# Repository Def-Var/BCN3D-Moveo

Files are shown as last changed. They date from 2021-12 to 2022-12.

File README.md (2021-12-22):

# DefVar Moveo
This project is forked from [BCN3d MOVEO](https://github.com/BCN3D/BCN3D-Moveo). I changed some parts for my purposes so that I can rebuild this project six years after its creation.
Please check out my [blog](https://def-var.net) where I post weekly about this project.

## Changes

Changed in Motor type results in new 3M2C and 3M2CC use the new Version instead

## 3D printing settings 
layer height: 0.2 mm
Material: PLA 
Infill: 15% 

# Original Moveo README.md
In the following, there is the original text from the BCN3D MOVEO README.md

## BCN3D MOVEO

This is the repository that contains the CAD files, the STL files, the user manual (with the assembly manual), the firmware, and the Bill of Materials of the BCN3D Moveo.
BCN3D Technologies keeps taking important steps in order to achieve his goal of bringing the digital manufacturing technology to everyone. In this occasion we are presenting the BCN3D Moveo, a robotic arm design from scratch and developed by our engineers in collaboration with the Departament d’Ensenyament from the Generalitat de Catalunya. Its structure is fully printed using additive manufacturing technologies and its electronics are controlled by the software Arduino.
Moveo, fully functional nowadays, has been born, as all the BCN3D Technologies products, with an open and educational wish.

### Why BCN3D Moveo

One of the Departament d’Ensenyament worries is the high price of the materials the grade students must use on their internships. Holding that in mind, an Open Source robotic arm, adaptable by the students and low cost reproducible could take several educational itineraries: mechanical design, automatism, industrial programing, etc.
Thus, the BCN3D Moveo should allow the educational centers to enjoy a modifiable and easily accessible for the students, at a price far lower than the usual industrial equipment they used to have to acquire, with enough output for training purposes.
As a Fundació CIM area, BCN3D Technologies shares its educational vocation. That is the reason why when the Departament d’Ensenyament contacted us in order to suggest and offer this project a year ago we didn’t hesitate on taking that opportunity.
Once we had the robotic arm designed and manufactured we started the last phase of the project, which consisted on an assembling and fine tuning workshop for 15 institutes around Catalonia, which took place in the BCN3D Technologies.
These institutes already have the BCN3D Moveo in their classrooms and workshops, and will have to present an internship program that proves their knowledge about the arm during September.

### Open Source Technology: Github

As we have done with all our developed produtcs, the BCN3D Moveo files will be available for everyone. Thanks to the platform Github, a website where users around the world share their designs, anyone will be able to obtain all the necessary information in order to assemble his own BCN3D Moveo at home.

Unlike the other BCN3D products, the Moveo won’t be commercialized. The project has been born and developed in order to make a move for the community progress starting from the Departament d’Ensenyament idea.
Nevertheless, BCN3D will fee all the Moveo know how on our Github account, as we have been doing with all the BCN3D Technologies products. Thus, the users will be able to find the bill of material (BOM), where all the needed components for the assembling of the arm come detailed, as the CAD designs, so anyone will be able to modify the BCN3D Moveo design as they wish.
Furthermore, the Github users will find the STL files for the structure printing and the assembling, fine tuning and firmware upload manuals, which will be available both in English and Spanish.

### Acknowledgements

This project is based on a project by [Andreas Hölldorfer](http://chaozlabs.blogspot.de/). You can see his original project on [Hackaday.io](https://hackaday.io/project/3800-3d-printable-robot-arm), [Github](https://github.com/4ndreas/BetaBots-Robot-Arm-Project/tree/master), [Youtube](https://www.youtube.com/channel/UCeFKz1UJUd5YuxS1ZikqYwA).

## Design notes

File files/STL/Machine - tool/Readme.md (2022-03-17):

# Not Orignial Parts

Changed:
- Servo Gear v3.stl

Added:
- Gripper Servo horn v4.stl

## Why?

Default 'Servo Gear' can't be mounted on a default servo horn. I added a custom servo horn.

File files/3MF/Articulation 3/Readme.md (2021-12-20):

# Changes
Changed the engine. See my [blog entry](https://def-var.net/project/diy-moveo-part-5-1-changes-3m2).

Please be aware that the entry is accessible after the 10.01.22

## 3M2C v1

The chamber for the engine is 6 mm bigger.

## 3M2C v1

The chamber for the enigner is 6 mm bigger.

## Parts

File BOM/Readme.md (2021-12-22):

# BOM 
for my [blog entries](https://def-var.net), I have split the BOM into three parts. 
- Part 1: [Components](https://github.com/Def-Var/Moveo/blob/master/BOM/BOM_Part1-Components.md)
- Part 2: [Fasteners](https://github.com/Def-Var/Moveo/blob/master/BOM/BOM_Part2-Fasteners.md)
- Part 3: [Printed Parts](https://github.com/Def-Var/Moveo/blob/master/BOM/BOM_Part3-Printed-parts.md)

Please note, that I changed some parts. For a detail description, see my [blog](https://def-var.net).

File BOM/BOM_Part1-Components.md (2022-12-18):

# Components
| BOM ID | Description | Quantity | Price[^1]  | Supplier[^2] | 
| --- | --- | --- | --- | --- |
| 4  | Power Supply 24V 480W | 1 | 32.99 | [Amazon](https://www.amazon.de/Schaltnetzteil-Netzteil-Transformator-Schaltwandler-Streifen/dp/B0896Z8Y3D/ref=sr_1_5) |
| 6  | Power converter 24V to 12V | 1 | 3.99  | [Amazon](https://www.amazon.de/LAOMAO-Step-up-Converter-Raspberry-DIY-Projects-1-St%C3%BCck/dp/B00HV59922/ref=sr_1_13)|
| 7  | Servo Motor 180° 55G TORQUE=13KG/CM | 1 | 21.99 | [Amazon](https://www.amazon.de/NEMA-17-Schrittmotor-Stepperonline-1-Planetengetriebe-3D-Drucker-Extruder/dp/B00QA5WSDG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)| 
| 8  | Gear Ratio 5:1 Planetary Gearbox Nema 17 Stepper 17HS19-1684S-PG5 ( step 0,35º , 2Nm, 1,68A) | 1 | 34.99 | [Amazon](https://www.amazon.de/STEPPERONLINE-Nema-Getriebemotor-Planetengetriebe-Schrittmotor/dp/B077ZPW7VT/ref=sr_1_7)|
| 15 | Ball Bearing 608ZZ 8mm x 22mm x 7mm | 10 | 1.10  | [M.D.](https://www.dold-mechatronik.de/Miniatur-Kugellager-608-ZZ-8x22x7-mm) | 
| 16 | Ball Bearing 625ZZ 5mm x 16mm x 5mm | 8 | 0.45  | [M.D](https://www.dold-mechatronik.de/Rillenkugellager-625-ZZ-5x16x5mm) | 
| 17 | Ball Bearing 624ZZ 4mm x 13mm x 5mm | 9 | 0.45  | [M.D.](https://www.dold-mechatronik.de/Rillenkugellager-624-ZZ-4x13x5mm)  | 
| 18 | Ball Bearing 623ZZ 3mm x 10mm x 4mm | 3 | 0.50  | [M.D.](https://www.dold-mechatronik.de/Rillenkugellager-623-ZZ-3x10x4mm) | 
| 19 | Brass insert M4 x 8mm (Pack of 10) | 1 | 4.39  | [Ebay](https://www.ebay.de/itm/173779404364)  | 
| 20 | Brass insert M3 x 6mm (Pack of 20) | 1 | 5.99  | [Ebay](https://www.ebay.de/itm/173779404364) | 
| 21 | Pulley T5, Bore 8mm, 14 tooth, 17mm width | 1 | 3.06  | [Aliexpress](https://de.aliexpress.com/item/32963062106.html) | 
| 22 | Pulley T5, Bore 5mm, 10 tooth, 17 mm width | 2 | 3.27  | [Aliexpress](https://de.aliexpress.com/item/32827985827.html)
| 24 | ZCOUPLING STEEL 5 TO 8 mm rigid | 1 | 8.50  | [M.D.](https://www.dold-mechatronik.de/Spielfreie-Wendelkupplung-Klemmnabenausfuehrung-JT16C-D16L23-500-800mm) | 
| 27 | Power supply cable IEC 1,8m | 1 | 7.99  | [Amazon](https://www.amazon.de/Naths-Hardware-Kaltger%C3%A4tekabel-Kaltger%C3%A4testecker-Schutzkontakt/dp/B06XG6Z7NL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) | 
| 29 | Cable Ties | 10 | 5.99  | [Amazon](https://www.amazon.de/Kabelbinder-Zugfestigkeit-Selbstsicherndes-Multifunktionale-Gartenarbeit/dp/B08PTT2C5M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) | 
| 32 | Wood Base - 550mm x 550mm x 16mm | 1 | - | H.S. | 
| 33[^3] | Breco belt T5, 16mm width, L **250cm** | 1 | 13.80 | [M.D.](https://www.dold-mechatronik.de/PU-Zahnriemen-T5-Breite-16mm-Meterware-Laenge-2-Meter) | 
| 34 | Pulley T5, Bore 10mm, 14 tooth, 17mm width | 2 | 3.27  | [Aliexpress](https://de.aliexpress.com/item/32963062106.html) | 
| 35 | Nema 23 stepper 3Nm 4,2A Ø 10 mm shaft | 2 | 25.21 | [Ebay](https://www.ebay.com/itm/392720416199) |
| 36 | Chrome steel smooth bar 140mm M8 | 1 | 1.10  | [M.D.](https://www.dold-mechatronik.de/Blankstahl-rund-8mm-h6-Material-C45-10503-geschliffen-ZUSCHNITT-bis-1200mm-5-EUR-m-04-EUR-pro-Schnitt) |
| 37 | Chrome steel smooth bar 121mm M8 | 1 | 1.01  | [M.D.](https://www.dold-mechatronik.de/Blankstahl-rund-8mm-h6-Material-C45-10503-geschliffen-ZUSCHNITT-bis-1200mm-5-EUR-m-04-EUR-pro-Schnitt) |
| 38 | Chrome steel smooth bar 80mm M8 | 1 | 0.80  | [M.D.](https://www.dold-mechatronik.de/Blankstahl-rund-8mm-h6-Material-C45-10503-geschliffen-ZUSCHNITT-bis-1200mm-5-EUR-m-04-EUR-pro-Schnitt) |
| 39 | Chrome steel smooth bar 50mm M8 | 1 | 0.65  | [M.D.](https://www.dold-mechatronik.de/Blankstahl-rund-8mm-h6-Material-C45-10503-geschliffen-ZUSCHNITT-bis-1200mm-5-EUR-m-04-EUR-pro-Schnitt) |
| 40 | Stepper Motor Driver DM 556 5,6 A | 2 | 17.29 | [Ebay](https://www.ebay.de/itm/353803925809)  |
| 41 | Stepper Motor Driver TB 6600 4 A 9 - 42V | 4 | 9.99  | [Ebay](https://www.ebay.de/itm/133963951405) |
| 42 | Teensy 4.0 | 1 | 24.45 | [Amazon](https://www.amazon.de/Teensy-DEV-13305-Development-Bootloader-Mikro-USB-Sketches/dp/B01BMRTZGE/ref=sr_1_1) |
| 43 | Nema 17 Stepper Motor 42BYGHW609, (1.7A, 1.8°,  4000 g·cm) | 2 | 14.99 | [Ebay](https://www.ebay.com/itm/381706411494) |
| 44 | Nema 14 Stepper Motor, B089Y48SWK, (1A, 1.8°,  2141 g·cm) | 1 | 15.99 | [Amazon](https://www.amazon.de/Iverntech-Schrittmotor-2-Phasen-4-adrig-Integriertem-CNC-Maschine/dp/B089Y48SWK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) |
| 1000 | End Splices | ~100 | - |  |
| 1001 | AWG20 Cable Red 2m | 1 | - |  |
| 1002 | AWG20 Cable Black 2m | 1 | - |  |
| 1003 | Arduino Nano | 1 | - | |
| 1004 | Arduino Nano Breakout Board | 1 | - |  |
| 1005 | 10 meters 4 channel RGB Wire (awg21) | 1 | - |  |
| 1006 | 10 meters 4 channel RGB Wire (awg18) | 1 | - |  |

H.S. – local hardware store

[M.D.](https://www.dold-mechatronik.de/) – Mechatronic Dold is a local Store. It would make me glade if you purchase some of your items there.  :) 

[^1]: Unit in € 
[^2]: Currently only EU Supplier be free to make a custom Suplier list and make a pull request ;) 
[^3]: 1x 70cm (Base / Module 1) 2x 44.8 cm (Module 2) 1x 44.6 cm (Module 3) 1x 27 cm (Module 4)

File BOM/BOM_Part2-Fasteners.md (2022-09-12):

# Fasteners 

|BOM ID|Description|Amount|
|--- |--- |--- |
|101|Screw M3 x 10|23|
|102|Screw M3 x 12|8|
|103|Screw M3 x 16|21|
|104|Screw M3 x 30|1|
|105|Screw M3 x 25|2|
|106|Screw M3 x 30|1|
|107|Screw M3 x 40|7|
|110|Screw M4 x 16|4|
|111|Screw M4 x 40|8|
|112|Screw M4 x 45|6|
|114|Screw M5 x 14|8|
|115|Screw M5 x 20|8|
|116|Screw M8 x 65|1|
|117|Screw M4 x 20|4|
|118|Nut M3|22|
|119|Nut M4|7|
|120|Locknut M4|22|
|121|Locknut M5|16|
|122|Locknut M8|2|
|123|Screw M4 x 20|1|
|124|Screw M3 x 8|4|
|125|Screw M4 x 30|4|
|127|Whaser M3|7|
|128|Whaser M4|8|
|129|Whaser M5|4|
|130|Screw M5 x 30 |
|1101 | M3 Locknut |4|

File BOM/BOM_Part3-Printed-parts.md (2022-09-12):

# Printed Parts

| BOM ID | Parts | File | Name | Amount | m | mm^3 | weight[^0] | price | time[^1] |
| --- | --- | --- | --- | --- | --- | --- | --- | --- | --- |
| 202 | Articulation 1 | | 1M1 | 1.00 | | 104682.95 | 129.81 | 3.78 €  | 00:11:13 |
| 203 | | | 1M2 | 1.00 | 75.66  | 181987.81 | 225.66 | 6.28 €  | 00:19:31 |
| 204 | | | 1M3 | 1.00 | 17.01  | 40911.15  | 50.73  | 1.41 €  | 00:04:41 |
| 205 | Articulation 2 | | 2M1 | 1.00 | 134.61 | 323784.49 | 401.49 | 11.17 € | 01:10:52 |
| 206 | | | 2M2H | 1.00 | 57.48  | 138251.49 | 171.43 | 4.77 €  | 00:15:10 |
| 207 | | | 2M2M | 1.00 | 57.41  | 138092.06 | 171.23 | 4.76 €  | 00:15:05 |
| 208 | | | T2M1C | 2.00 | 8.39 | 20186.8 | 25.03  | 0.70 €  | 00:02:00 |
| 210 | Articulation 3 | | 3M1 | 1.00 | 84.88  | 204163.81 | 253.16 | 7.04 €  | 00:21:59 |
| 233 | | | 3MC v1 | 1.00 | 45.12  | 108536.4  | 134.59 | 3.74 €  | 00:12:23 |
| 234 | | | 3MCC v1 | 1.00 | 47.33  | 113845.58 | 141.17 | 3.93 €  | 00:13:04 |
| 212 | | | T3M1 | 1.00 | 1.92 | 4630.04 | 5.74 | 0.16 €  | 00:00:39 |
| 213 | Articulation 4 | | 4M1 | 1.00 | 36.81  | 88546.19  | 109.80 | 3.05 €  | 00:10:07 |
| 214 | | | 4M2 | 1.00 | 12.76  | 30699.4 | 38.07  | 1.06 €  | 00:03:41 |
| 215 | | | 4M2C | 1.00 | 13.82  | 33235.94  | 41.21  | 1.15 €  | 00:04:13 |
| 216 | | | T4M1 | 1.00 | 1.06 | 2541.97 | 3.15 | 0.09 €  | 00:00:38 |
| 217 | Gripper A | Gripper-A | Top plate | 1.00 | 12.97  | 31184.63  | 38.67  | 1.08 €  | 00:04:05 |
| 218 | A | Gripper-A | Bottom plate | 1.00 | | | | | |
| 219 | B | Gripper-B | Cilinder | 2.00 | 3.69 | 8875.77 | 11.01  | 0.31 €  | 00:01:15 |
| 220 | B | Gripper-B | Pivot arm | 2.00 | | | | | |
| 221 | A | Gripper-A | Gripper left | 1.00 | | | | | |
| 222 | A | Gripper-A | Gripper right | 1.00 | | | | | |
| 223 | B | Gripper-B | Idol gear | 1.00 | | | | | |
| 224 | B | Gripper-B | Servo gear | 1.00 | | | | | |
| 228 | Base | | Posets Base | 1.00 | 108.88 | 242639.8  | 300.87 | 8.31 €  | 01:00:43 |
| 229 | Cover | Covers | Tapa 2M1 | 2.00 | 15.35  | 36913.35  | 45.77  | 1.27 €  | 00:03:51 |
| 230 | | Covers | Tapa 3M1 | 2.00 | | | | | |
| 231 | | Covers | Tapa 4M1 | 2.00 | | | | | |
| 232 | | Covers | Tapa TBB | 1.00 | | | | | |
| 235 | Sleeve | Sleeves | Sleeve M8 | 2.00 | 2.54 | 6117.33 | 7.59 | 0.21 €  | 00:01:04 |
| 236 | | Sleeves | Sleeve M5 | 8.00 | | | | | |
| 237 | Gripper | Gripper-A | Gripper Servo horn | 1.00 | | | | | |
| 1200 | PSU Case |  PSU Case |  PSU Case | 1.00 | | | | | |
| 1201 | DIN RAIL PSU Bracket|  DIN RAIL PSU Bracket |  DIN RAIL PSU Bracket | 1.00 | | | | | |

## Total 
| Weight[^0] | Time[^1] | Price[^2] |
| --- | --- | --- |
| 2.31 | 08:12:09 | 69.3 |

[^1]: Format: dd:hh:mm
[^0]: Unit: kg
[^2]: Unit Euro and assuming that 1kg Material costs €30

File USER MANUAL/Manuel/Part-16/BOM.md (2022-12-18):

| BOM ID | Quantity | Name | 
| --- | --- | --- |
| 29 | a lot | Cable Ties | 
| 1205 | 1 | 10 meters 4 channel RGB Wire (awg21) |  
| 1206 | 1 | 10 meters 4 channel RGB Wire (awg18) |

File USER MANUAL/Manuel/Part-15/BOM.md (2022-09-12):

| BOM ID | Quantity | Name | 
| --- | --- | --- |
| 101 | 4 | M3x10 Screw |
| 1101  | 4 | M3 Locknut |
| 1200 | 1 | PSU Case |
| 1201 | 1 | DIN Rail PSU Bracket |
| 120  | 1 | AWG20 Cable 15cm Red |
| 120 | 1 | AWG20 Cable 15cm Black|
| 1000  | 20[^2] | end splices |
| 6 | 1 | Power Converter 24V to 12V |
| 1003 | 1 | Arduino Nano | 
| 1004 | 1 | Arduino Nano Breakout Board |

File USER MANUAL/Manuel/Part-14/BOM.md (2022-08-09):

| BOM ID | Quantity | Name | 
| --- | --- | --- |
| -[^1] | 1 | IEC320 C14 Plug |
| -[^1] | 3 | XT60E-M |
| -[^1] | 6 | Screw M2.5x10 |
| -[^1] | 7 | Screw M4x10 |
| 120 | 2 | Locknut M4 |
| 120 | 2 | Locknut M3 |
| -[^1] | 2 | Countersunk screw M3x10 DIN 965 | 
| -[^1] | 2 | PSU Brackets (Print) | 
| -[^1] | 1 | PSU Case (Print) | 
| -[^1] | 1 | 1m AWG18 Cable RED | 
| -[^1] | 1 | 1m AWG18 Cable BLACK | 
| -[^1] | 20[^2] | end splices |

[^1]: Currently there is no global custom BOM. 
[^2]: it's a guess

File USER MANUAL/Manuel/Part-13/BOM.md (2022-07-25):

| BOM ID | Quantity | Name | 
| --- | --- | --- |
| -[^1] | 2 | Screw M3 x 10 mm |
| -[^1] | 2 | Locknut M3 |
| -[^1] | 2 | Spacer | 
| -[^1] | 1 | [Power Distribution Board](https://www.amazon.de/-/en/gp/product/B0814B5P5M/ref=ppx_yo_dt_b_asin_title_o02_s00?ie=UTF8&psc=1) | 
| -[^1] | 1 | DIN Railbracket Power Distrubter | 
| -[^1] | 1 | 1m AWG20 Cable RED | 
| -[^1] | 1 | 1m AWG20 Cable BLACK | 
| -[^1] | 20[^2] | end splices |

[^1]: Currently there is no global custom BOM. 
[^2]: it's a guess

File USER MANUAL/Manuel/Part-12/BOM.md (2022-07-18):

| BOM ID | Quantity | Name | 
| --- | --- | --- |
| -[^1] | 16 | Screw M4 x 10 mm |
| -[^1] |  2 | Screw M5 x 40 mm |
| -[^1] | 16 | M4 lock nut | 
| -[^1] | 4 | M4 Washer | 
| -[^1] | 4 | DIN Rail Bracket TB6600 | 
| -[^1] | 2 | DIN Rail Bracket DM556 | 
| -[^1] | 2 | DIN Rail Mount | 
| -[^1] | 1 | DIN Rial 35 x 7,5 length: 55 mm |

[^1]: Currently there is no global custom BOM.

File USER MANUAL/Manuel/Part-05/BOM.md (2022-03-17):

| BOM ID | Quantity | Name | 
| --- | --- | --- |
| 101 | 1 | Screw M3 x 10 mm |
| 103 | 13 | Screw M3 x 16 mm | 
| 118 | 8 | M3 Nut | 
| 127 | 7 | M3 Washer | 
| 217 | 1 | Top plate | 
| 220 | 2 | Pivot arm |
| 221 | 1 | Left gripper | 
| 222 | 1 | Right gripper | 
| 223 | 1 | Idol gear | 
| 224 | 1 | Servo gear |
| 218 | 1 | Bottom plate | 
| 219 | 2 | Sleeve | 
| 237 | 1 | Gripper Servo horn |

[^1]: I modifight this version to fit wit the motor

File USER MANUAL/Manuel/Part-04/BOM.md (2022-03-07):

| BOM ID | Quantity | Name | 
| --- | --- | --- |
| 14 | 1 | Smooth bar 80 mm |
| 15 | 3 | Bearing 8 x 22 x 7 | 
| 18 | 3 | Bearing 3 x 10 x 4 | 
| 20 | 8 | Brass insert M3 | 
| 22 | 1 | Pulley T5, Bore 5mm, 10 tooth, 17 mm width | 
| 44 | 1 | Nema 14 Stepper Motor, B089Y48SWK, (1A, 1.8°, 2141 g·cm) | 
| 102 | 8 | Screw M3 x 12 mm |
| 104 | 1 | Screw M3 x 20 mm | 
| 105 | 3 | Screw M3 x 25 mm |
| 106  | 1 | Screw M3 x 30 mm |
| 118 | 5 | M3 Nut | 
| 120 | 3 | M4 Locknut |
| 122 | 1 | M8 Locknut | 
| 124 | 4 | Screw M3 x 8 mm | 
| 214 | 1 | 4M2 | 
| 215 | 1 | 4M2C |
| 216 | 1 | T4M |
| 213[^1] | 1 | 4M1 |
| 231 | 2 | 4M1 | 
| 232 | 1 | TBB | 

[^1]: I modifight this version to fit wit the motor

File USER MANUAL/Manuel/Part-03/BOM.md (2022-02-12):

| BOM ID | Quantity | Name | 
| --- | --- | --- |
| 8 | 1 | Nema 17 R1:5 Motor |
| 13 | 1 | Smooth bar 114 mm | 
| 15 | 3 | Bearing 8 x 22 7 | 
| 17 | 3 | Bearing 4 x 14 x 5 |
| 20 | 6 | M3 inserts |
| 21 | 1 | 8mm Pulley | 
| 23[^2] | 1 | Rod bar L 42 mm Diameter 8 mm  |
| 24 | 1 | Coupling 8mm - 5mm |
| 43 | 1 | Nema 17 Stepper Motor 42BYGHW609, (1.7A, 1.8°, 4000 g·cm) |
| 101 | 8 | Screw M3x10 |
| 102 | 6 | Screw M3x12 | 
| 107 | 7 | Screw M3x40 |
| 110 | 4 | Screw M4x16 mm |
| 118 | 7 | M3 Nut | 
| 119 | 1 | M4 Nut | 
| 123 | 1 | Screw M4x20 mm |
| 210 | 1 | 3M1 |
| 210A / 233 [^1] | 1 | 3M2C |
| 211 / 234 [^1] | 1 | 3M2CC | 
| 212 | 1 | T3M1 | 
| 230 | 2 T3M1 | 

[^1]: These are modifight versions for the stepper 42BYGHW609. Please check out this [post](https://def-var.net/project/diy-moveo-part-5-1-changes-3m2/)
[^2]: This should be a threaded rod.

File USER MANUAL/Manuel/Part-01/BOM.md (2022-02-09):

| BOM ID | Quantity | Name | 
| --- | --- | --- |
|015|2| Ball Bearing 608ZZ 8mm x 22mm x 7mm |
| 016| 8 | Ball Bearing 625ZZ 5mm x 16mm x 5mm |
| 022| 1 | Pulley T5, Bore 5mm, 10 tooth, 17 mm width |
| 032 | 1 | Wood Base - 550mm x 550mm x 16mm |
| 043 | 1 | Nema 17 Stepper Motor 42BYGHW609, (1.7A, 1.8°,  4000 g·cm)  |
| 101 | 4 | Screw M3 x 8mm |
| 111 | 4 | Screw M4 x 40mm |
| 115 | 8 | Screw M5 x 20mm |
| 116 | 1 | Screw M8 x 65mm |
| 120 | 8 | M4 Locknut|
| 121 | 12 | M5 Locknut |
| 125 | 4 | Screw M4 x 30mm |
| 128 | 8 | Washer M4 |
| 129 | 4 | Washer M5 |
| 130[^1] | 4 | Screw M5 x 30mm |
| 202 | 1 | 1M1 |
| 203 | 1 | 1M2 |
| 204 | 1 | 1M3 |
| 228| 4 | Base post |
| 235| 1 | Sleeve M8 |
| 236| 8 | Sleeve M5 |
---
[^1]: Is not in the orginal BOM but in the 3D-Model this screw is used to mount the base posts.

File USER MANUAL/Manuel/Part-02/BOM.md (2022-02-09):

| BOM ID | Quantity | Name | 
| --- | --- | --- |
| 17 | 6 | Bearing 4 x 13 x 5 | 
| 19 | 2 | M4 Brass inserts |
| 20 | 6 | M3 Brass inserts |
| 21 | 2 | Bearing 8 x 22 x 7 |
| 33 | 2 | Breco belt T5, 16mm width, L 44.8cm |
| 34 | 2 | Pulley T5, Bore 10mm, 14 tooth, 17mm width | 
| 35 | 2 | Nema 23 stepper 3Nm 4,2A Ø 10 mm shaft | 
| 36 | 1 | Chrome steel smooth bar 140mm M8 |
| 101 | 6 | Screw M3 x 10 |
| 105 | 2 | Screw M3 x 25 |
| 111 | 4 | Screw M4 x 40 |
| 114 | 8 | Screw M5 x 14 |
| 117 | 2 | Screw M4 x 20 |
| 118 | 2 | M3 Nut | 
| 119 | 6 | M4 Nut  |
| 120 | 4 | M4 Locknut | 
| 121 | 8 | M5 Locknut | 
| 205 | 1 | 2M1 |
| 206 | 1 | 2M2M |
| 207 | 1 | 2M2H | 
| 208 | 1 | T2M1D |
| 209 | 1 | T2M1I |
| 229 | 2 | T2M1 |

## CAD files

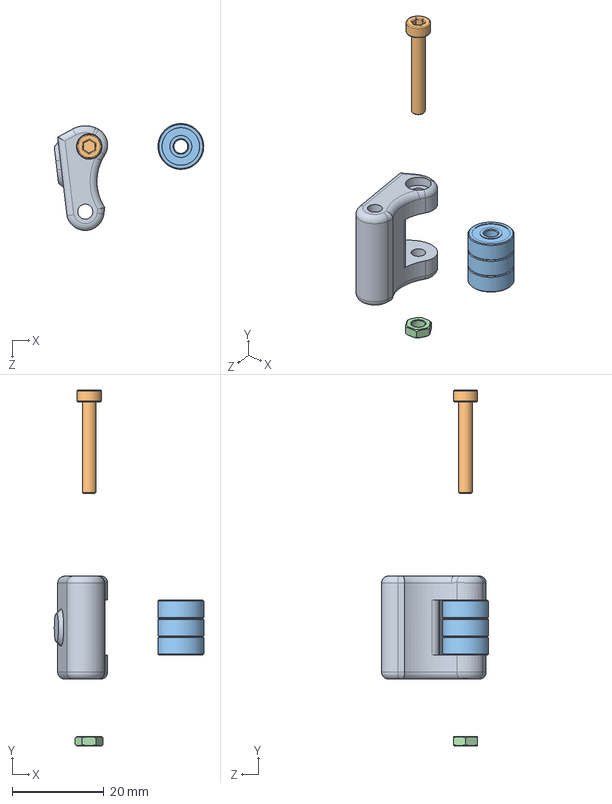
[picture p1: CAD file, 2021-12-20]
files/CAD/SLDPRT/M1 Tensor D.SLDASM
32.6 x 77.7 x 23.3 mm
T4M1E
M3x20
Bearing 3Bore 10Ext 4Height x 3
M3 Nut

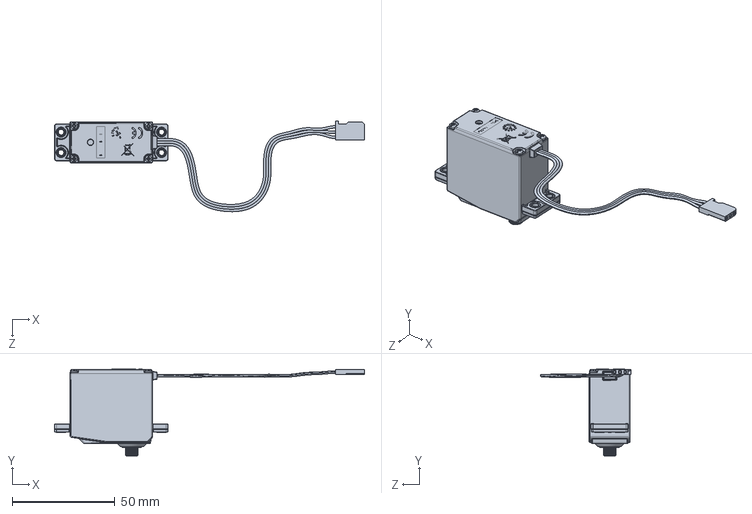
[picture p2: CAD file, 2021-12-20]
files/CAD/SLDPRT/2.SLDASM
151.2 x 42.3 x 44.1 mm

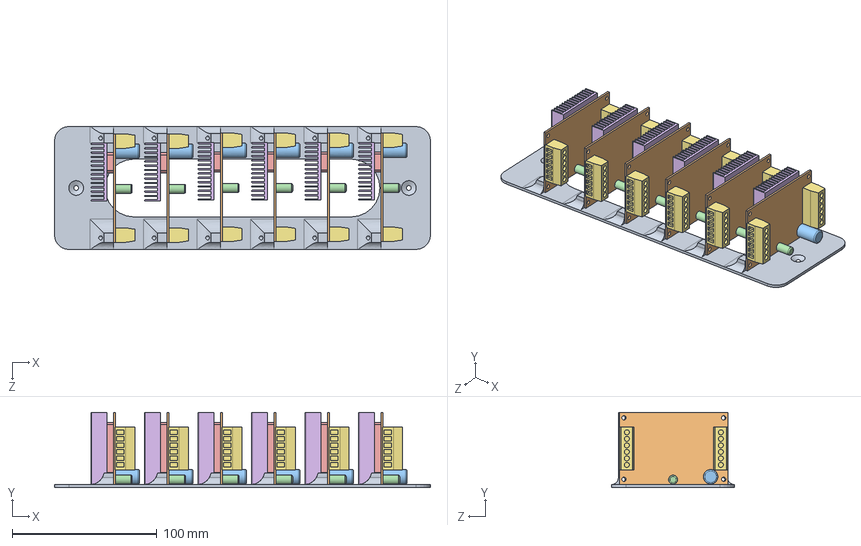
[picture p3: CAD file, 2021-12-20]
files/CAD/SLDPRT/Drivers Support Assembly B.SLDASM
260.0 x 52.0 x 85.0 mm
Suport Drivers E
PCB TB6560 x 6
Capacitor 1 x 6
Capacitor 2 x 6
Chip x 6
Sink x 6
Terminal x 12

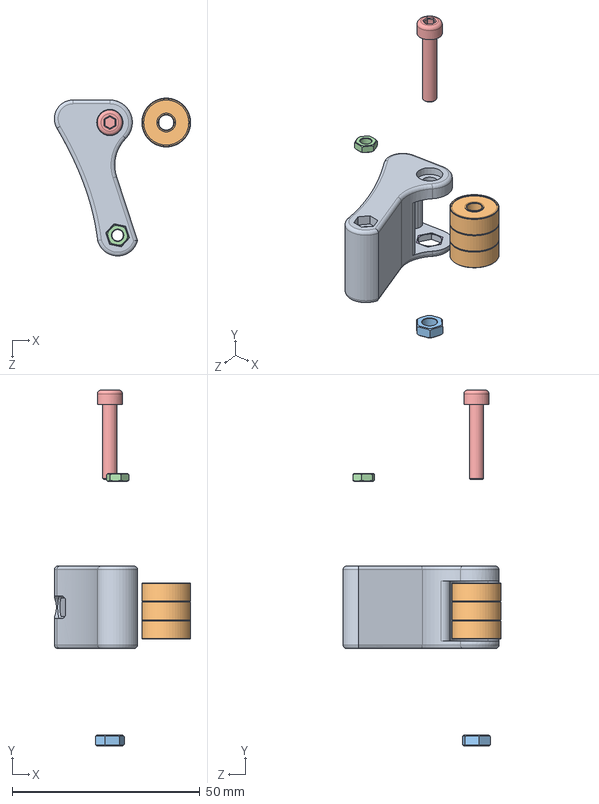
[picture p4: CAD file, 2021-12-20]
files/CAD/SLDPRT/Tensor D.SLDASM
36.3 x 94.7 x 42.0 mm
T2M1BD
Bearing 4Bore 13Ext 5 x 3
M4 Nut
M3 Nut
M4x20
Arandela

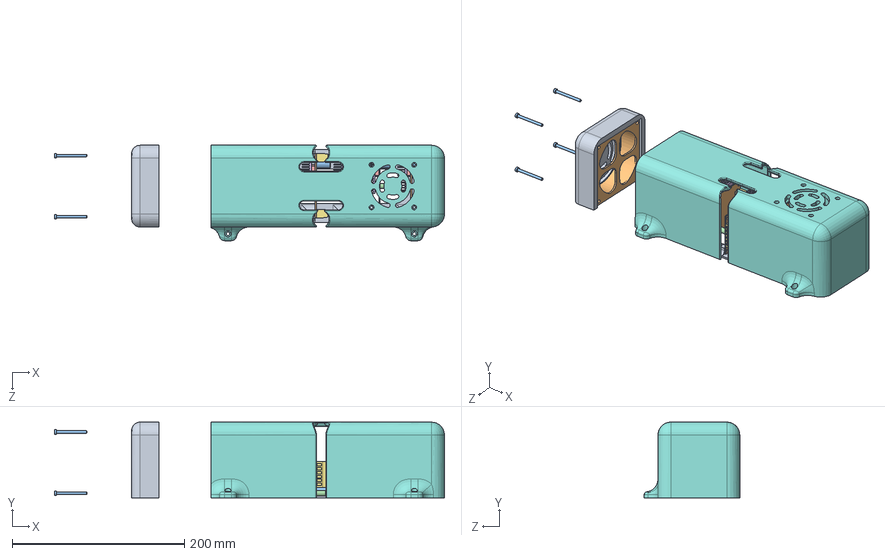
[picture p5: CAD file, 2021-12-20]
files/CAD/SLDPRT/Box Assembly B.SLDASM
453.0 x 88.0 x 111.0 mm
Suport Drivers E
PCB TB6560 x 6
Capacitor 1 x 6
Capacitor 2 x 6
Chip x 6
Sink x 6
Terminal x 12
Box C
Fan Module
Fan
M3x35 x 4

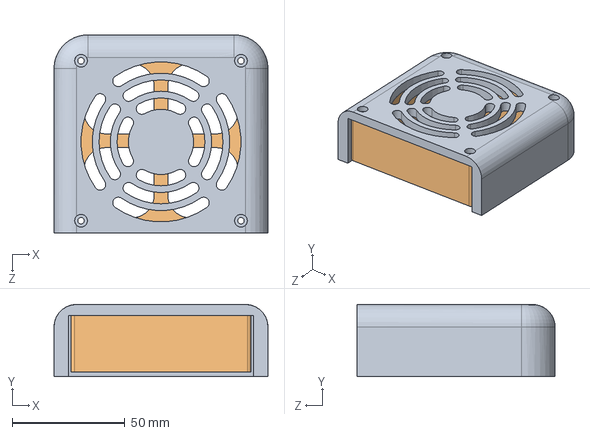
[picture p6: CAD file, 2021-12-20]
files/CAD/SLDPRT/Module Fan Assembly.SLDASM
95.0 x 32.0 x 88.0 mm
Fan Module
Fan

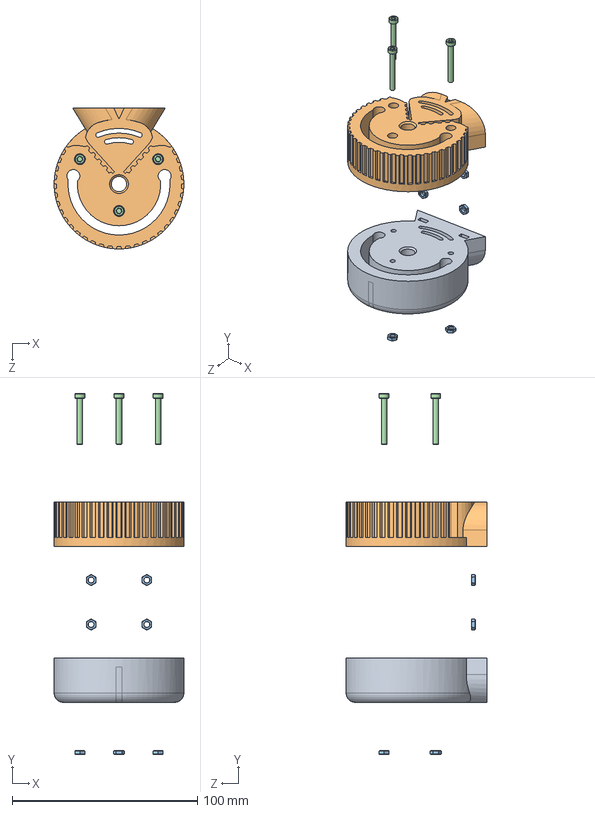
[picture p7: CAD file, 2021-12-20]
files/CAD/SLDPRT/4M2.SLDASM
70.0 x 194.7 x 76.0 mm
4M2B
4M2CB
M3 Nut x 7
M3x25 x 3

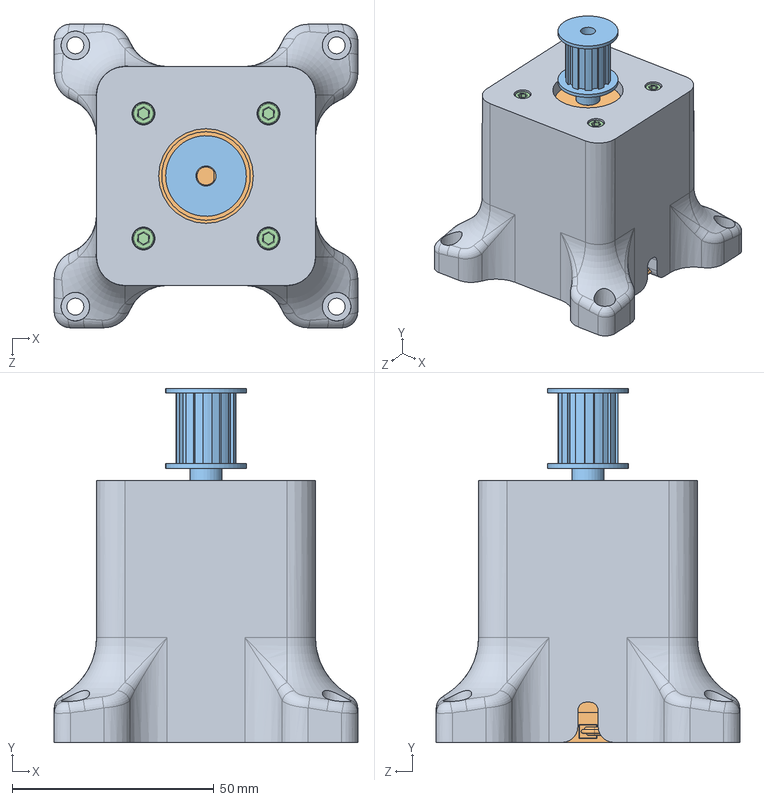
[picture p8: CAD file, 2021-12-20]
files/CAD/SLDPRT/1M3.SLDASM
75.3 x 87.8 x 75.3 mm
1M3A
Nema 17 Llarg
Pulley M5
M3x10 x 4

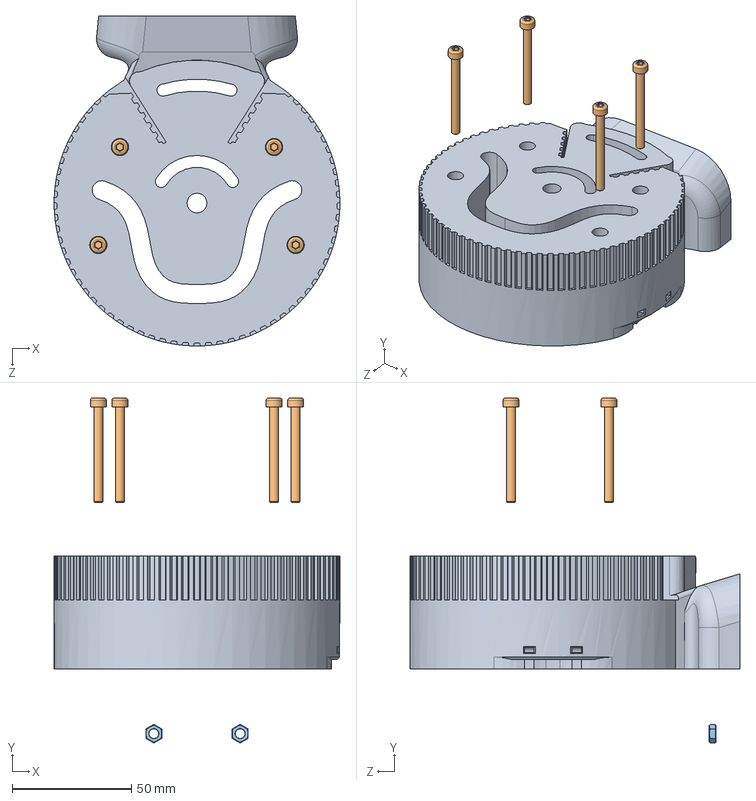
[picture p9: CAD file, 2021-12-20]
files/CAD/SLDPRT/2M2M assembly.SLDASM
120.0 x 144.8 x 138.5 mm
2M2MA
M4x40 x 4
M4 Nut x 2

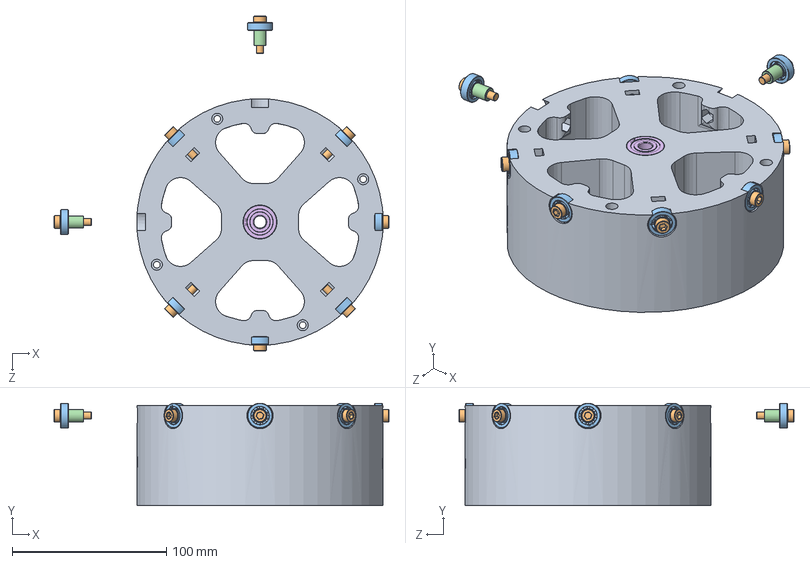
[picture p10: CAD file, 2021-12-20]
files/CAD/SLDPRT/Rotary Plate.SLDASM
217.5 x 66.5 x 217.5 mm
1M2A
M5x20 x 8
Bearing 5mm x 8
Spacer M5x10 x 8
Spacer M8x20
8mm Bearing x 2

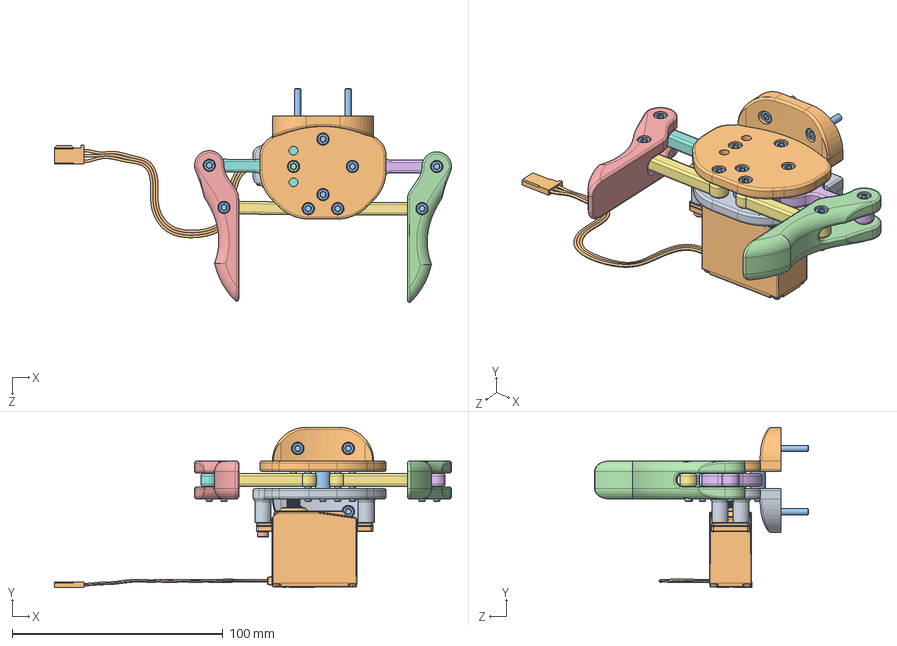
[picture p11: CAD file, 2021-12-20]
files/CAD/SLDPRT/Gripper B Assembly.SLDASM
188.5 x 76.1 x 101.5 mm
Bottom Plate C
Top Plate C
Cilinder x 2
Gripper Left B
Gripper Right B
Idol Gear B
Pivot Arm B x 2
Servo Gear B
M3 Nut x 9
Servo Futaba S3003
M3x16 x 13
M3x8

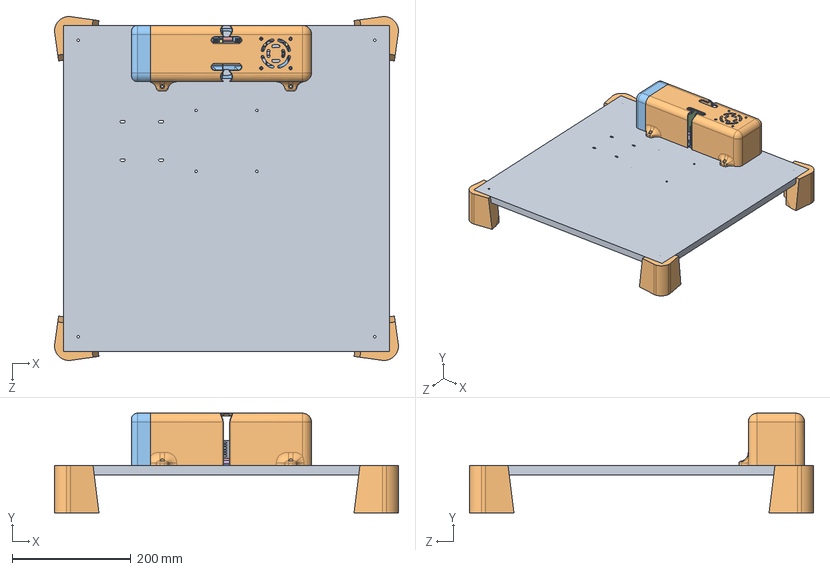
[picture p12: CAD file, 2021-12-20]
files/CAD/SLDPRT/Base assembly.SLDASM
579.8 x 168.0 x 579.8 mm
Base fusta
Potes base B x 4
Suport Drivers E
PCB TB6560 x 6
Capacitor 1 x 6
Capacitor 2 x 6
Chip x 6
Sink x 6
Terminal x 12
Box C
Fan Module
Fan

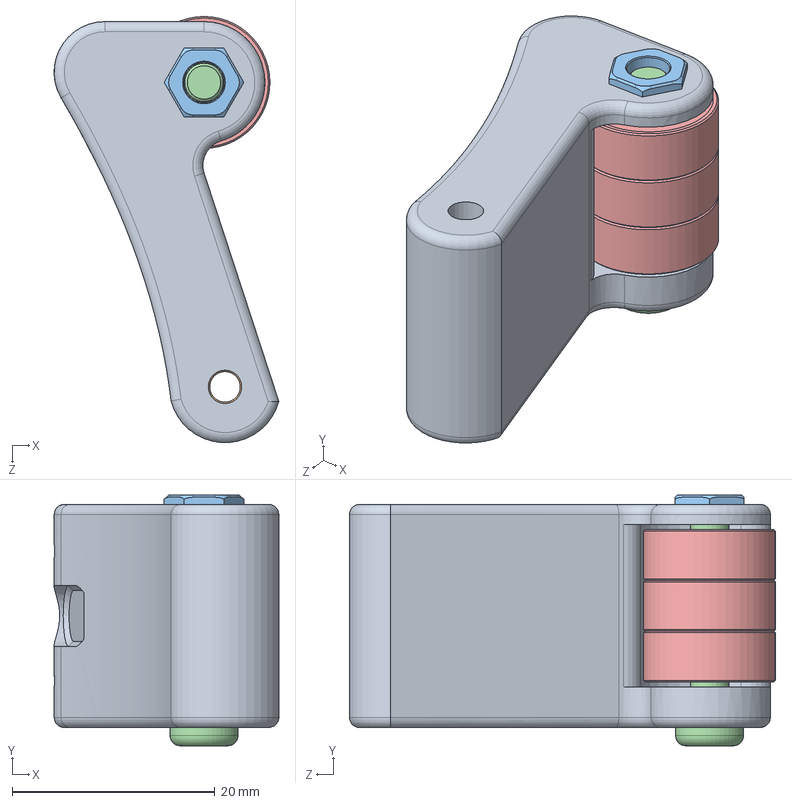
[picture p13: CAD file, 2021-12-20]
files/CAD/SLDPRT/Tensor I.SLDASM
22.2 x 24.7 x 42.0 mm
T2M1BI
M3 Nut
M4 Nut
M4x20
Bearing 4Bore 13Ext 5 x 3

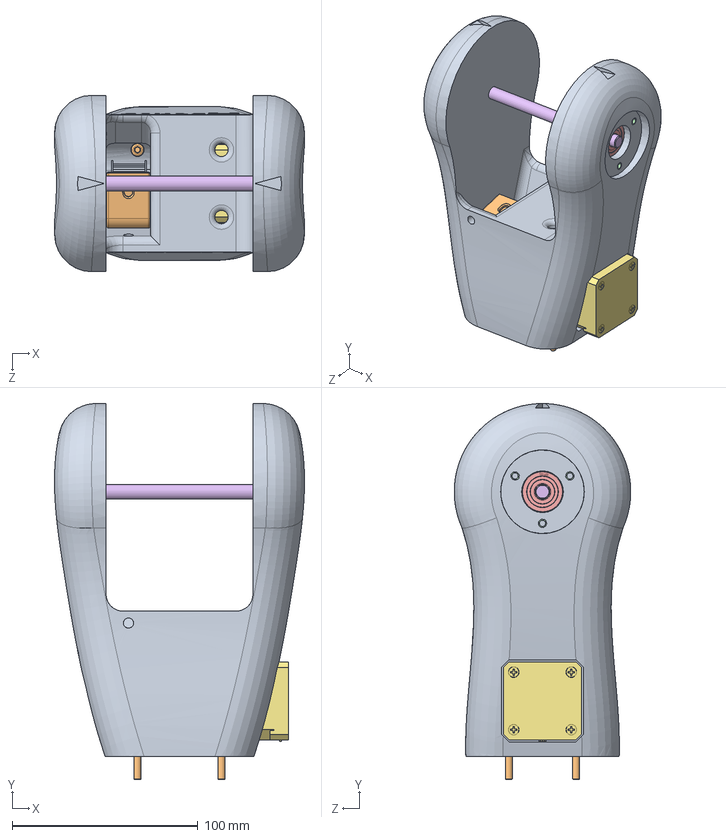
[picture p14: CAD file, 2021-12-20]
files/CAD/SLDPRT/3M1.SLDASM
134.6 x 202.4 x 95.0 mm
3M1D
T3M1C
M4 Nut
M4x20
Bearing 4Bore 13Ext 5 x 3
M3x40
Nema 17 Reductor
M3x12 x 4
Pulley 8mm IGNIS
M4x16 x 4
M3 Nut
Brass insert M3 x 6
8mm Bearing x 2
Smooth bar 8mm x 121mm

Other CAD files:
files/CAD/SLDPRT/2M2 assembly.SLDASM
files/CAD/SLDPRT/Sistema rodaments.SLDASM
files/CAD/SLDPRT/2M1 assembly.SLDASM
files/CAD/SLDPRT/Driver.SLDASM
files/3MF/Articulation 1/1M1B.3mf
files/3MF/Articulation 1/1M2A.3mf
files/3MF/Articulation 1/1M3.3mf
files/3MF/Articulation 1/Sleeve M5 8x10 v2.3mf
files/3MF/Articulation 1/Sleeve M8 12x20 v2.3mf
files/3MF/Articulation 2/2M1.3mf
files/3MF/Articulation 2/2M2HA.3mf
files/3MF/Articulation 2/2M2MA.3mf
files/3MF/Articulation 2/T2M1C.3mf
files/3MF/Articulation 3/3M1D.3mf
files/3MF/Articulation 3/3M2C v1.3mf
files/3MF/Articulation 3/3M2CC v1.3mf
files/3MF/Articulation 3/T3M1C.3mf
files/3MF/Articulation 4/4M1D.3mf
files/3MF/Articulation 4/4M2B+4M2C.3mf
files/3MF/Articulation 4/4M2B.3mf
files/3MF/Articulation 4/4M2CB.3mf
files/3MF/Articulation 4/T4M1E.3mf
files/3MF/Base/Potes base.3mf
files/3MF/Cover/T2M1C.3mf
files/3MF/Cover/T3M1C.3mf
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

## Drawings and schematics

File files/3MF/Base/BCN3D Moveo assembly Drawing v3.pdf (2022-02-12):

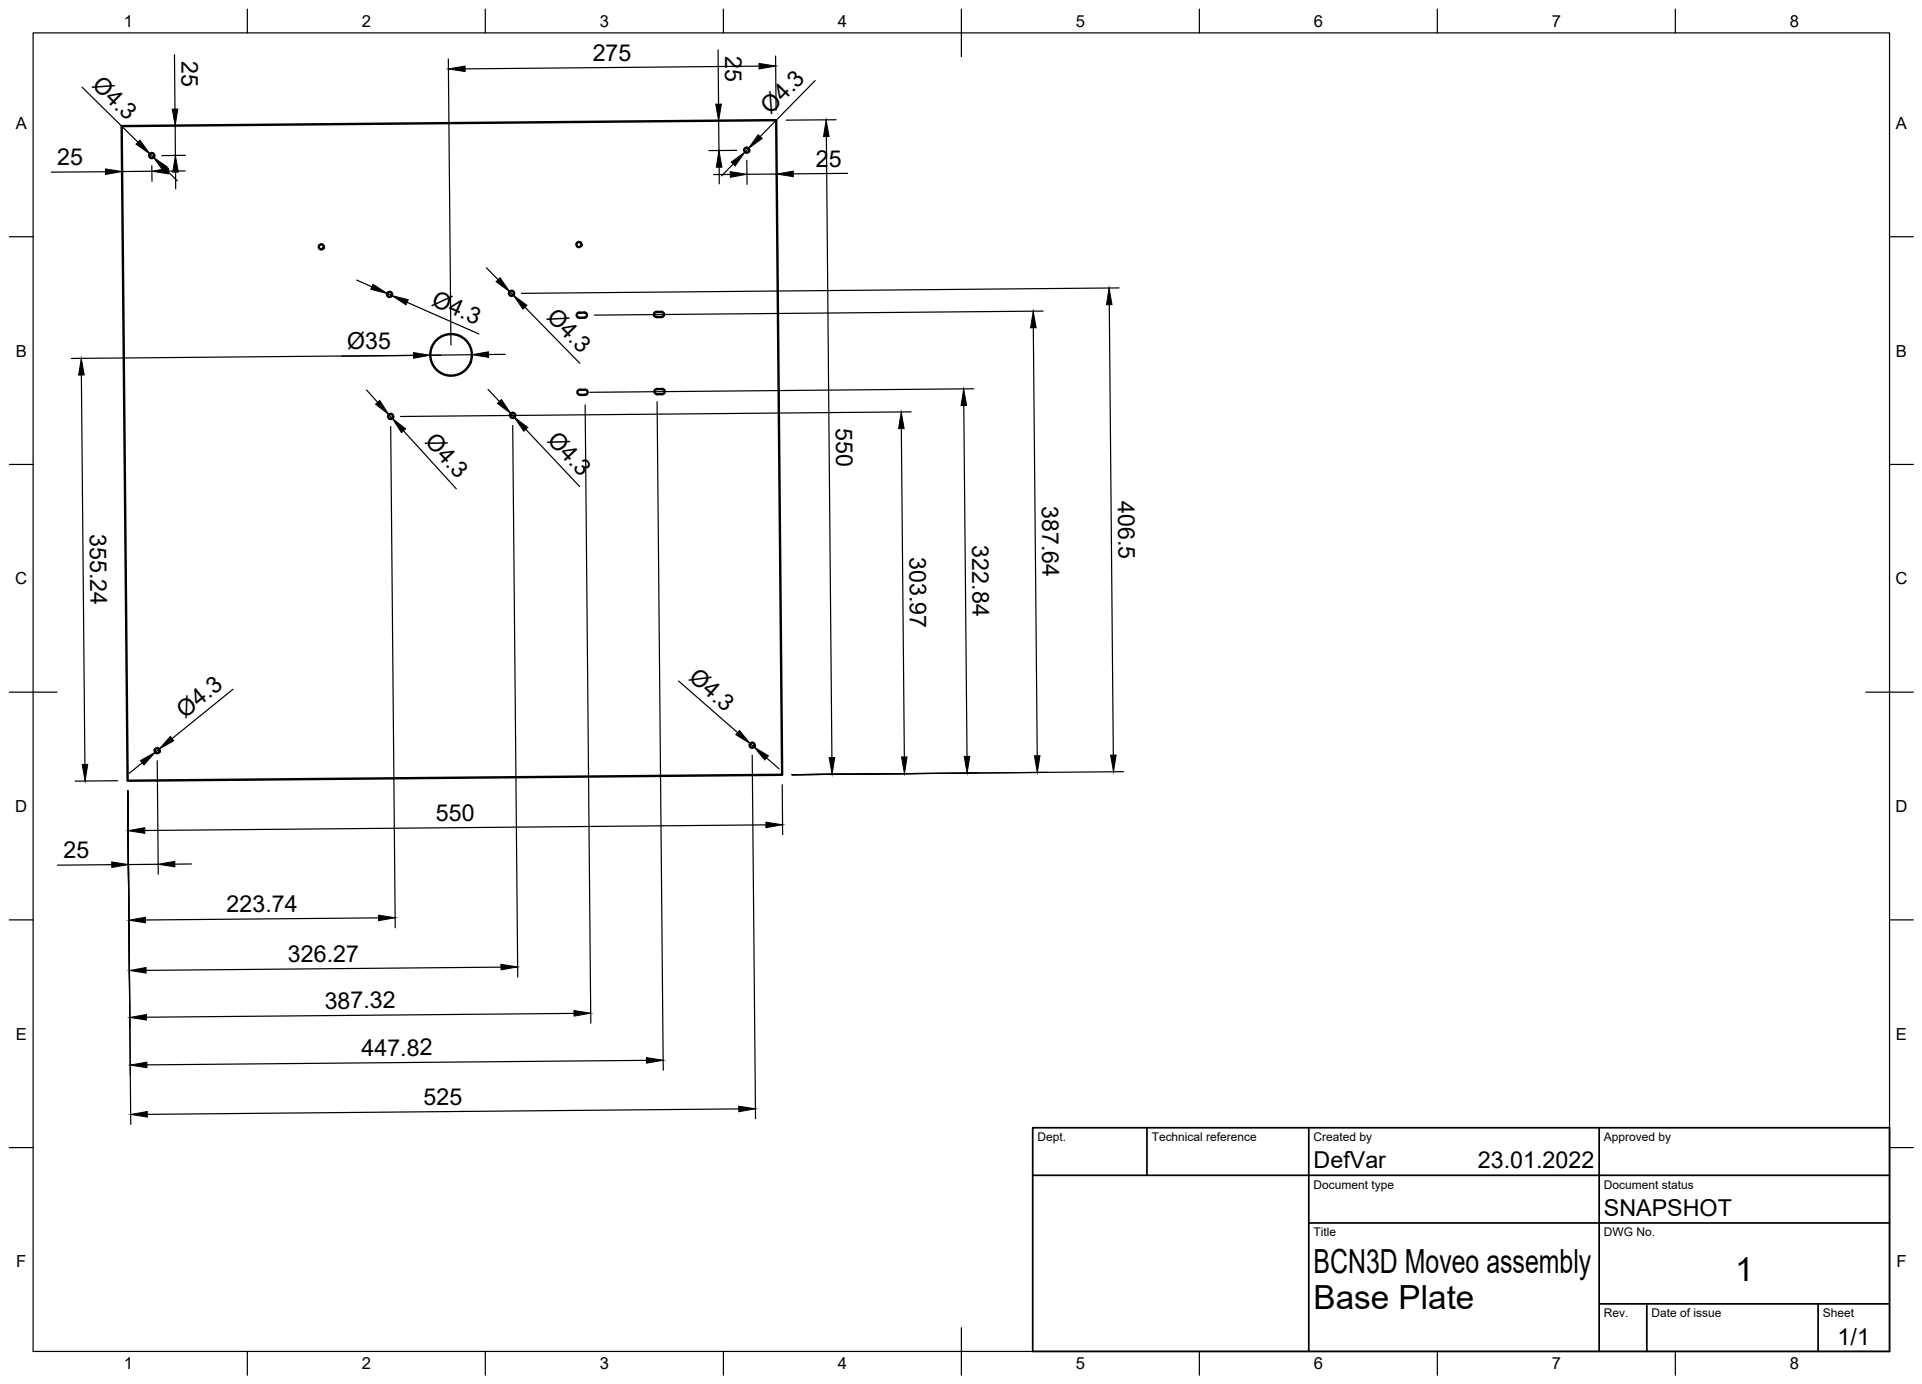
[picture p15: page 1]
Title; DWG No.; Rev.; Date of issue; Sheet; Base Plate; BCN3D Moveo assembly

Dept. | Technical reference | Created by DefVar 23.01.2022 | Approved by

Document type | Document status SNAPSHOT

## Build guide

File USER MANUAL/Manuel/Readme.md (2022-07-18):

# Assembly Manuel Parts 
This section is for the manuel parts posted on my [blog](https://def-var.net/moveo)

 - [DIY Moveo Part 7: Rotary Plate](https://def-var.net/project/diy-moveo-part-7-assembly-of-rotary-plate/)
 - [DIY Moveo Part 8: Module 2](https://def-var.net/project/diy-moveo-part-8-module-2/)
 - [DIY Moveo Part 9: Module 3](https://def-var.net/project/diy-moveo-part-9-module-3/)
 - [DIY Moveo Part 10: Module 4](https://def-var.net/project/diy-moveo-part-10-module-4/)
 - [DIY Moveo Part 11: The Gripper](https://def-var.net/project/diy-moveo-part-11-the-gripper/)

After Moveo Part 7 - 11 the orginal Moveo build is done. 
Because I used some differend drivers (because I used differend engines).
I can't use the orginal electronics housing. The next few parts are for a custom
housing and uses materials that aren't nessasally in the orignal BOM.

- [DIY Moveo Part 12: electronics mount](https://def-var.net/project/diy-moveo-part-12-electronics-mount/)
- [DIY Moveo Part 12.1: electronics mount installation](https://def-var.net/project/diy-moveo-part-12-1-electronics-mount-installation/)

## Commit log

2021-12-20 Added 3M2C and 3M2CC
    [1M1.STL, 1M2.STL, 2M2H.STL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]
2021-12-20 Added Sleeves BOM ID 30 / 31 as print
    [Sleeve M5 8x10 v2.3mf, Sleeve M8 12x20 v2.3mf]
2021-12-20 Added 3mf files
    [1M1B.3mf, 1M2A.3mf, 1M3.3mf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]
2021-12-20 First update
    [1M1B.SLDPRT, 1M2A.SLDPRT, 1M3.SLDASM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]
2021-12-21 Added print time readme.md
2021-12-22 Added BOM part 3
2021-12-22 Update footprint
2021-12-22 Added BOM
2021-12-22 Update BOM
2021-12-22 Added CAD-Models for Sleeves
    [Sleeve M5 8x10 v2.f3d, Sleeve M8 12x20 v2.f3d]
2021-12-23 BOM_Part3 ',' -> '.' & Update BOM ID 203
2022-01-22 Added first part BOM (snapshot)
2022-01-22 Update Part1 BOM
2022-02-02 Update BOM.md (M5 Screws for posts and more)
2022-02-02 Add <hr> in BOM.md to make the blog-post better
2022-02-09 Update BOM Part 01 && Added BOM Part 02
2022-02-12 Update BOM ID 33
    Belt length from 180 cm to 250 cm
    I have not yet built Module 4 I did now exactly how much meters are needed, but
    I already used up nearly 2 meters...
2022-02-12 Update some files
    [4M2B+4M2C.3mf, Potes base.3mf, T2M1BD v1.3mf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]
2022-02-12 Add BOM Part 3 v1
2022-02-12 Updated Module 3 Belt length
2022-03-09 Added parts for part 11
    [Servo horn.stl]
2022-03-17 Update Gripper Parts
    [Gripper Servo horn v4.stl, Servo Gear v3.stl, Servo Gear.STL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]
2022-03-17 Added Servo horn
    [Gripper Drawing v1.csv]
2022-06-25 Update for Part 12
    [DIN Rail Mount v3.stl, DIN Railbracket DM556 v4.stl, DIN Railbracket TB 6600 v3.stl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]
2022-07-25 Added Part 13 to the mix
    [DIN Railbracket Power Distrubter v3.stl]
2022-09-10 Add PSU Case and Bracket
    [DIN PSU Rail bracket v5.stl, PSU Case v69.stl]
2022-09-12 DIY Moveo Part 15: Motherboard
    [DIN Railbracket uC v8.stl, PCB Spacer v1.stl]
2022-12-18 Added Part 16
    [Gripper Drawing v1.csv]
2023-02-12 Update DIN Rail Mount from Version v3 to v6
    [DIN Rail Mount v3.stl, DIN Rail Mount v6.stl]
